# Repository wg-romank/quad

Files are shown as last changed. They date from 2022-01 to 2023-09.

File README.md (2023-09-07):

# Overview

Brushed quadcopter design. Main goal for this project is to develop a platform for testing flight controller algorithms, mainly stabilisation, out of least amount of off-the-shelf parts. It is built around 4-channel MOSFET driver YYNMOS-4 and uses Bluetooth for communication.

While there are plenty quadcopter designs out there, they seem to fall in two main categories: custom flight controllers with BLDC motors and FPV-setups with brushed motors and ready-made flight controllers. This repo tries to adress lack of materials around brushed designs with custom flight controllers.

Top | Bottom
:--:|:------:
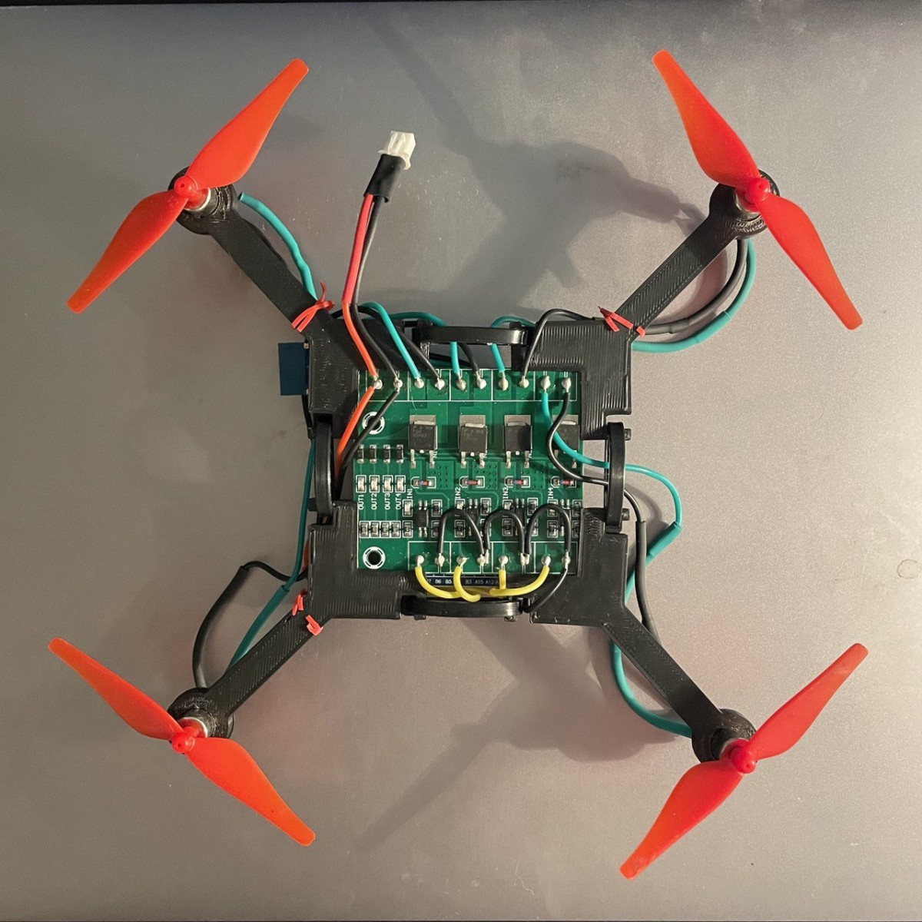
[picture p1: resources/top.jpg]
Top view
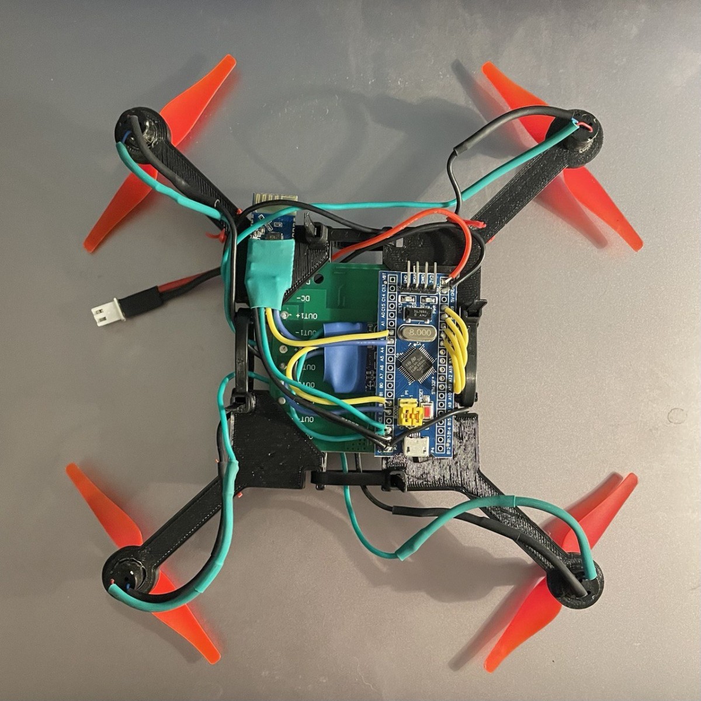
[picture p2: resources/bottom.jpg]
Bottom view
|

# Crates

Project is split in 3 crates as well as Godot project.

`flight-controller` targets stm32f103 boards and includes logic handling pwm signals for motor control, IMU, bluetooth communication via UART.

`client-util` targets PC and mainly provides helper functions for communication via Bluetooth with RFCOMM.

`common` is a holds shared functionality between above crates and includes types describing message format for communication between stm32 device and host.

Godot is mainly used as a tool to build interactive UI serving as mission control for the drone.

# Hardware

1. Main board - stm32f103c8
2. IMU with Gyro and Accelerometer - mpu6050
3. Telemetry and control via Bluetooth - JDY-31-SPP
4. Power delivery - YYNMOS-4 MOSFET driver
5. Battery - Syma X5C 3.7V 600mah or any other rated 25C
6. Motors - 4 x 8520 coreless motor
7. Propellers - 4 x 55mm (2 x CW + 2 x CCW), shaft diameter must match of motors
8. [Frame](resources/part.stl) - 3d printed in 4 identical pieces, might need to adjust tolerances

Total weight assembled ~ 82g

# Motors & IMU orientation

<TODO>

# Wiring diagram



Power for bluetooth module and IMU can be connected to main board directly for convenience.

`GNDX` terminals on mosfet driver can be soldered together and connected to `GND` on main board.

Important note is since motors need to spin in opposite directions, one needs to pay attention connecting motor wires to mosfet driver.

Motors polarity described as `+` and `-` and is reversed for 2nd and 4th motor.

Battery terminals are shared betewen `DC+/-` connections on mosfet driver and `3V/GND` on main board.

# Todos

- [x] Share state types between client and device libraries
- [ ] Map controller to throttle correction and try to fly without stabilisation
- [ ] Test naive stabilisation
- [ ] Send state telemetry from device
- [ ] Update mission control UI to include state
- [ ] Check if Tokio or any other runtime can help to buffer telemetry on the client in separate task/thread

# Potential upgrades

- IMU with mangetometer to correct for yaw drift
- IR sensor to measure distance to the ground
  - Upgrade stabilisation to implement "Hover" mode
- Swap Bluetooth for RC to increase range
- Downward facing camera to detect position drift
- Toroidal propeller to improve noise / efficiency?

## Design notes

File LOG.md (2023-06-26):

31/05/23
========
- arrived 5x stm32 boards, swapping board seem to fix previous issues with flashing
- had a weird issue of gyro task not spawning after switching uart bluetooth pins
- switched off the board gave it a rest & the issue is not observed anymore
- tested with 25c battery, seems too weak to lift off, but did hover a little
- battery showed 3v with multimeter - probably almost discharged
- unable to check how much current drawn in total, seems multimeter is having a cap of 1a or just above that
- made a little harness out of thread to do stabilization; pretty fun to fire off the motors

todo:
- fully charge battery & re-do max thrust test
- order a different battery with more punch
- could start to implement PID with thread harness already

08/06/23
========
- testing thrust with fully charged battery showed promising results
- found issue in wiring forcing one of the motors to spin in wrong direction (:O)
- restructured commands format to accomodate for different types of actions, not just throttle
  - included `borsh` to automatically derive encoders / decoders
- added commands to enable / disable main board led and stabilisation
- shorted battery (T_T)
- implemented naive stabilisation
  - found issues in implementation since IMU is upside down and some of axises are flipped

todo:
- write a page on how naive stabilisation works
- check stabilisation effect on light throttle
- implement moving pitch / roll with gamepad axis for control

11/06/23
========
- fixed stabilisation direction, seems to be engaging correct motors based on tilt now
- fixed wiring order & updated flight controller pwm code
- shorted battery again (X_X)
- restructured project a bit with better namings
- added testing mode for motors to only enable single one
  - currently it runs in order 1,2,3,4 then enabling all

todo:
- motors seem to draw power unevenly (could be due to limited current of damaged battery)
- get a new battery and check current for all motors in single mode (possible with limiting current on mutlimeter?)
- motor can stuck in 'on' mode even when not enabled (parasitic capacitance?)
  - turning motor on again seems to unstuck them (could be solved when undamaged battery is installed?)

14/06/23
========
- crashed drone while testing power output with fresh and fully charged battery
- one of props is slighly bent
- doulbe check & triple-check the battery connection when charging
- some issues found with sending commands to quad, probably this is causing motors to keep spinning and other stuff
- uneven power improves when graudally increasing throttle, probably control task is running at too high frequency so mosfet driver does not have enough time to respond
- re-watched talk on flight controller stabilisation, missing part is PI controller for rate of change for gyros, not just angles

todos:
- improve communication to limit number of messages sent and ensure commands do not clog the queue
- reduce control frequency, possibly split gyro into separate task to do median filtering on acc with high frequency
- implement heartbeat & throttle cutoff for safety

26/06/23
========
- implemented masking to enalbe specific motors for testing
- tested current draw with lab bench DC: 1 + 3 and 2 + 4 motors current draw is different of up to 1 amp
- implemented basic safety with RTC to set throttle to 0 if last command was sent more than a second ago

todos:
- map controller stick to motors correction & try to fly

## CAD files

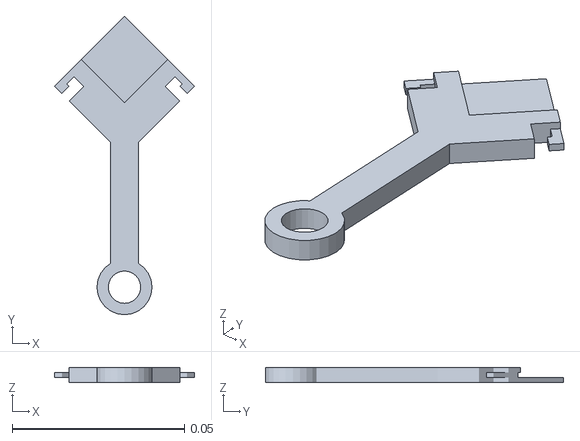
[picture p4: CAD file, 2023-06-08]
resources/part.stl
0.0407 x 0.0867 x 0.0045

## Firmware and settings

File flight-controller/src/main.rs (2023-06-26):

// #![deny(unsafe_code)]
#![no_std]
#![cfg_attr(not(doc), no_main)]

mod spatial;

use panic_rtt_target as _;

#[rtic::app(device = stm32f1xx_hal::pac, dispatchers = [WWDG, RTC])]
mod app {
    use nalgebra::Vector3;
    use rtt_target::{rprintln, rtt_init_print};

    use stm32f1xx_hal::device::USART2;
    use stm32f1xx_hal::dma::CircBuffer;
    use stm32f1xx_hal::gpio::{Output, PushPull, CRH};
    use stm32f1xx_hal::rtc::Rtc;
    use stm32f1xx_hal::timer::{Timer, Tim4NoRemap, Event as TEvent};
    use stm32f1xx_hal::{
        gpio::{
            Pin,
            gpiob::{PB10, PB11},
            Alternate, OpenDrain,
        },
        i2c::{BlockingI2c, DutyCycle, Mode},
        pac::{I2C2, TIM4},
        prelude::*,
        pwm::{C1, C2, C3, C4, PwmChannel},
        serial::{Config, Serial, Tx, Event, RxDma2},
    };

    use systick_monotonic::*;

    use crate::spatial::{SpatialOrientationDevice, GYRO_FREQUENCY_HZ};
    use common::{SpatialOrientation, QuadState};
    use common::COMMANDS_SIZE;
    use common::postcard::{from_bytes, to_vec};
    use common::heapless;



    use mpu6050::Mpu6050;

    #[monotonic(binds = SysTick, default = true)]
    type MyMono = Systick<100>;

    type MPU = Mpu6050<BlockingI2c<I2C2, (PB10<Alternate<OpenDrain>>, PB11<Alternate<OpenDrain>>)>>;
    type PWM = (
        PwmChannel<TIM4, C1>,
        PwmChannel<TIM4, C2>,
        PwmChannel<TIM4, C3>,
        PwmChannel<TIM4, C4>,
    );

    #[shared]
    struct Shared {
        state: common::QuadState,
        mpu: Option<(MPU, Vector3<f32>, SpatialOrientation)>,
        rtc: Rtc,
    }

    #[local]
    struct Local {
        recv: Option<CircBuffer<[u8; COMMANDS_SIZE], RxDma2>>,
        usart2_tx: Tx<USART2>,
        pwm: PWM,
        led: Pin<Output<PushPull>, CRH, 'C', 13>,
    }

    #[init]
    fn init(cx: init::Context) -> (Shared, Local, init::Monotonics) {
        rtt_init_print!();

        let dp = cx.device;
        let cp = cx.core;

        let mut flash = dp.FLASH.constrain();

        let rcc = dp.RCC.constrain();
        let mut afio = dp.AFIO.constrain();

        let clocks = rcc.cfgr.freeze(&mut flash.acr);

        let mono: MyMono = Systick::new(cp.SYST, clocks.sysclk().0);

        // RTC
        let mut pwr = dp.PWR;
        let mut backup = rcc.bkp.constrain(dp.BKP, &mut pwr);
        let rtc = Rtc::new(dp.RTC, &mut backup);

        // BLUETOOTH
        let mut gpioa = dp.GPIOA.split();
        let usart2_pins = (
            gpioa.pa2.into_alternate_push_pull(&mut gpioa.crl),
            gpioa.pa3,
        );

        let mut usart2 = Serial::usart2(
            dp.USART2,
            usart2_pins,
            &mut afio.mapr,
            Config::default().baudrate(9600.bps()),
            clocks,
        );
        usart2.listen(Event::Idle);

        let dma1 = dp.DMA1.split();
        let (usart2_tx, rx) = usart2.split();
        let rrx = rx.with_dma(dma1.6);

        let buf = cortex_m::singleton!(: [[u8; COMMANDS_SIZE]; 2] = [[0; COMMANDS_SIZE]; 2]).unwrap();
        let rx_transfer = rrx.circ_read(buf);

        // GYRO
        let mut gpiob = dp.GPIOB.split();
        let i2c_pins = (
            gpiob.pb10.into_alternate_open_drain(&mut gpiob.crh),
            gpiob.pb11.into_alternate_open_drain(&mut gpiob.crh)
        );

        let i2c2 = BlockingI2c::i2c2(
            dp.I2C2,
            i2c_pins,
            Mode::Fast {
                frequency: 400_000.hz(),
                duty_cycle: DutyCycle::Ratio16to9,
            },
            clocks,
            1000,
            10,
            1000,
            1000,
        );

        // LED
        let mut gpioc = dp.GPIOC.split();
        let mut led = gpioc.pc13.into_push_pull_output(&mut gpioc.crh);
        led.set_high();

        // TIMERS
        let mut telemetry_tim = Timer::tim2(dp.TIM2, &clocks)
                    .start_count_down(2.hz());
        telemetry_tim.listen(TEvent::Update);

        let mut gyro_tim = Timer::tim3(dp.TIM3, &clocks).start_count_down(GYRO_FREQUENCY_HZ.hz());
        gyro_tim.listen(TEvent::Update);

        // PWM
        let pb6 = gpiob.pb6.into_alternate_push_pull(&mut gpiob.crl);
        let pb7 = gpiob.pb7.into_alternate_push_pull(&mut gpiob.crl);
        let pb8 = gpiob.pb8.into_alternate_push_pull(&mut gpiob.crh);
        let pb9 = gpiob.pb9.into_alternate_push_pull(&mut gpiob.crh);

        let pwm = Timer::tim4(dp.TIM4, &clocks).pwm::<Tim4NoRemap, _, _, _>(
            (pb6, pb7, pb8, pb9), &mut afio.mapr, 200.hz()
        );
        let mut channels = pwm.split();
        channels.0.enable();
        channels.1.enable();
        channels.2.enable();
        channels.3.enable();


        let mpu = Mpu6050::new(i2c2);
        // the issue is that when board is offline i2c delay does not seem to work causing it to fail initialisation
        // todo: find a good way to handle it with i2c config
        mpu_init::spawn_after(1.secs(), mpu);

        (
            Shared {
                state: QuadState::default(),
                mpu: None,
                rtc,
            },
            Local {
                recv: Some(rx_transfer),
                usart2_tx,
                pwm: channels,
                led,
            },
            init::Monotonics(mono),
        )
    }

    #[task(shared = [mpu])]
    fn mpu_init(mut cx: mpu_init::Context, mut mpu: MPU) {
        cx.shared.mpu.lock(|m| {
            mpu.init().expect("unable to init MPU6050");
            let offset = (0..2000)
                .flat_map(|_| mpu.get_gyro().ok())
                .reduce(|l, r| (l + r) / 2.0)
                .expect("no calibration measurements");
            let angles = mpu.get_acc_angles().expect("unable to get acc angles");

            let spatial_orientation = SpatialOrientation::new(angles);

            *m = Some((mpu, offset, spatial_orientation))
        })
    }

    #[task(binds = TIM3, local = [pwm, led], shared = [mpu, state, rtc], priority = 1)]
    fn gyro(cx: gyro::Context) {
        let mpu = cx.shared.mpu;
        let state = cx.shared.state;
        let rtc = cx.shared.rtc;

        (mpu, state, rtc).lock(|m, state, rtc| {
            if let Some((mpu, offset, s)) = m {
                let raw_gyro = mpu.get_gyro().expect("unable to get gyro");
                let angles = mpu.get_acc_angles().expect("unable to get acc angles");

                s.adjust(raw_gyro - *offset, angles);
                rprintln!("{:?}", s);
                rprintln!("current time {:?}", rtc.current_time());

                let t = state.throttle(rtc.current_time());
                let led_on = state.led;
                let mode = &state.mode;
                let stab_on = state.stabilisation;

                let [dx1, dx2, dx3, dx4] = if stab_on {
                    s.compute_corrections(&state.desired_orientation)
                } else {
                    [0., 0., 0., 0.]
                };

                let max_duty: f32 = u16::MAX as f32;
                cx.local.pwm.3.set_duty((mode.is_x1_enabled() * max_duty * (t + dx1)) as u16);
                cx.local.pwm.2.set_duty((mode.is_x2_enabled() * max_duty * (t + dx2)) as u16);
                cx.local.pwm.1.set_duty((mode.is_x3_enabled() * max_duty * (t + dx3)) as u16);
                cx.local.pwm.0.set_duty((mode.is_x4_enabled() * max_duty * (t + dx4)) as u16);

                if led_on {
                    cx.local.led.set_low();
                } else {
                    cx.local.led.set_high();
                }
            }
        });
    }

    #[task(binds = TIM2, local = [usart2_tx], shared = [state], priority = 1)]
    fn telemetry(mut cx: telemetry::Context) {
        // todo:
        cx.shared.state.lock(|s| {
            let tx: &mut Tx<USART2> = cx.local.usart2_tx;
            let packet: heapless::Vec<u8, 30> = to_vec(s).expect("unable to serialize to buff");
            IntoIterator::into_iter(packet)
                .for_each(|byt| { nb::block!(tx.write(byt)).unwrap() });
            rprintln!("State sent")
        })

        // cx.shared.state.lock(|state| {
        //     rprintln!("T {:?}", state);
        // });
    }

    #[task(binds = USART2, local = [recv], shared = [state, rtc], priority = 2)]
    fn on_rx(cx: on_rx::Context) {
        if let Some(rx) = cx.local.recv.take() {
            let (buf, rx) = rx.stop();

            if let Ok(command) = from_bytes(&buf[0]) {
                let state = cx.shared.state;
                let rtc = cx.shared.rtc;

                (state, rtc).lock(|state, rtc| {
                    let time = rtc.current_time();
                    state.update(command, time)
                });
            }

            let (rx, channel) = rx.release();
            rx.clear_idle_interrupt();
            let rx = rx.with_dma(channel);

            cx.local.recv.replace(rx.circ_read(buf));
        }
    }
}

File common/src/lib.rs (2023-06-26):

#![cfg_attr(not(feature = "godot"), no_std)]
#[cfg(feature = "godot")]
pub use gdnative;
#[cfg(feature = "godot")]
use gdnative::prelude::{ToVariant, FromVariant};

pub use serde::{Serialize, Deserialize};
pub use postcard;
pub use heapless;

#[derive(Debug, Serialize, Deserialize)]
#[cfg_attr(feature = "godot", derive(ToVariant, FromVariant))]
pub struct SpatialOrientation {
    pub pitch: f32,
    pub roll: f32,
}

impl SpatialOrientation {
    pub fn compute_corrections(&self, desired: &SpatialOrientation) -> [f32; 4] {
        // axes swapped
        // pitch goes from - to =
        // roll goes from + to -
        let e_p = (desired.pitch - self.pitch) / PI;
        let e_r = (desired.roll - (- self.roll)) / PI;

        let delta_x1 = e_p + e_r;
        let delta_x2 = e_p - e_r;
        let delta_x3 = -e_p - e_r;
        let delta_x4 = -e_p + e_r;

        [
            delta_x1, delta_x2, delta_x3, delta_x4
        ]
    }
}

#[derive(Debug, Serialize, Deserialize)]
#[cfg_attr(feature = "godot", derive(ToVariant, FromVariant))]
pub struct QuadState {
    // time from RTC is in seconds
    pub last_command_time: u32,
    throttle: f32,
    pub led: bool,
    pub stabilisation: bool,
    pub desired_orientation: SpatialOrientation,
    pub mode: MotorsModeCombined,
    // todo:
    // orientation: SpatialOrientation
}

impl Default for QuadState {
    fn default() -> Self {
        Self {
            last_command_time: 0,
            throttle: 0.0,
            led: false,
            stabilisation: false,
            desired_orientation: SpatialOrientation { pitch: 0., roll: 0. },
            mode: MotorsModeCombined(0b1111),
        }
    }
}

impl QuadState {
    pub fn throttle(&self, time: u32) -> f32 {
        if self.last_command_time.abs_diff(time) <= 1 {
            self.throttle
        } else {
            0.0
        }
    }
    pub fn update(&mut self, command: Commands, time: u32) {
        self.last_command_time = time;
        match command {
            Commands::Throttle(t) =>
                self.throttle = t,
            Commands::Led(on) =>
                self.led = on,
            Commands::Stabilisation(on) =>
                self.stabilisation = on,
            Commands::Angles(p, r) =>
                self.desired_orientation = SpatialOrientation { pitch: p, roll: r },
            Commands::SwitchMode(m) =>
                self.mode.0 = m,
        }
    }
}

use core::f32::consts::PI;

#[repr(u8)]
#[derive(Serialize, Deserialize, Debug)]
#[cfg_attr(feature = "godot", derive(ToVariant, FromVariant))]
pub enum MotorsMode {
    X1 = 0b1000,
    X2 = 0b0100,
    X3 = 0b0010,
    X4 = 0b0001
}

#[derive(Serialize, Deserialize, Debug)]
#[cfg_attr(feature = "godot", derive(ToVariant, FromVariant))]
pub struct MotorsModeCombined(u8);

impl MotorsModeCombined {
    pub fn is_x1_enabled(&self) -> f32 {
        (self.0 & MotorsMode::X1 as u8) as f32
    }

    pub fn is_x2_enabled(&self) -> f32 {
        (self.0 & MotorsMode::X2 as u8) as f32
    }

    pub fn is_x3_enabled(&self) -> f32 {
        (self.0 & MotorsMode::X3 as u8) as f32
    }

    pub fn is_x4_enabled(&self) -> f32 {
        (self.0 & MotorsMode::X4 as u8) as f32
    }
}

#[derive(Serialize, Deserialize, Debug)]
#[cfg_attr(feature = "godot", derive(ToVariant, FromVariant))]
pub enum Commands {
    Throttle(f32),
    Stabilisation(bool),
    Led(bool),
    Angles(f32, f32),
    SwitchMode(u8)
}

pub const COMMANDS_SIZE: usize = core::mem::size_of::<Commands>();

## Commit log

2022-01-07 Add device code to the same repo
2022-01-11 Getting started with PWM
2022-01-11 Restore gyro
2022-01-19 A bit better error handling & trying to do mission control
    [lib.rs]
2023-05-14 Update rust toolchain; add test code to trigger max duty pwm; remove enabling pin
2023-05-31 Swap usart pins for bluetooth
    [main.rs]
2023-06-07 Fix task preemption, todo: cleanup initialisation
    [lib.rs, main.rs]
2023-06-08 Wiring diagram; pwm order fix
    [part.stl]
2023-06-09 Add testing mode for motors
2023-06-10 Add missing bits to wiring
2023-06-14 Connect throttle mode buttons; introduce timer; set rest of pwms to 0 when single testing motors
2023-06-26 Set motors mode as mask; - todo: test different motor configurations enabled max current drain
